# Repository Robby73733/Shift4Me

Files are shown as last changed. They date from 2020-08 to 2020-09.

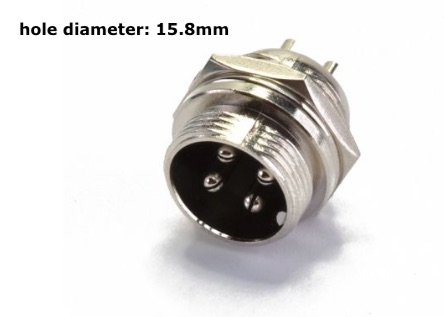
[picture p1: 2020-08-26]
installation/pics_18-22/Pic_22.JPG

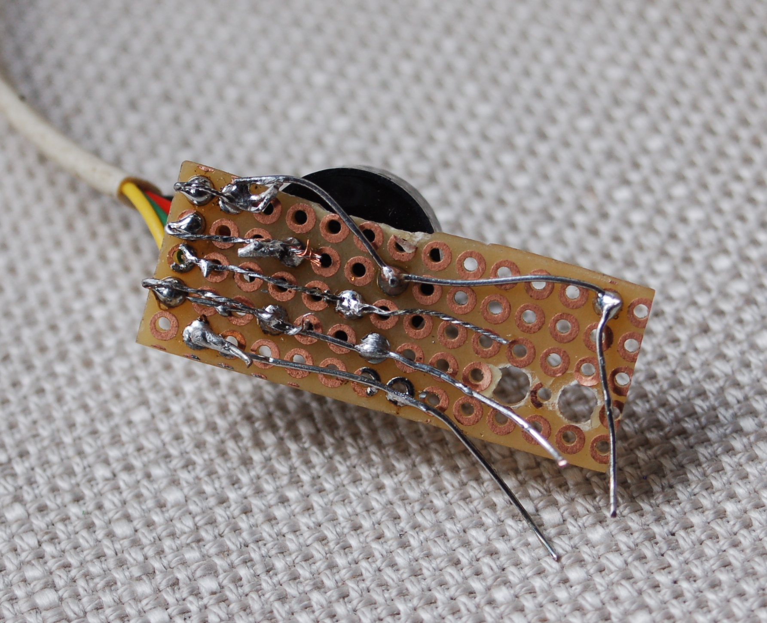
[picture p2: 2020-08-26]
installation/pics_1-17-building-manual/Pic_7.JPG

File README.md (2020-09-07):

# Shift4Me
Automatic Gear Shifting

www.shift4me.com

[heise.de news](https://www.heise.de/news/Shift4Me-Automatische-Fahrradschaltung-mit-Arduino-4873946.html) [2020/08/25]

[chip.de news](https://www.chip.de/news/Fahrrad-Hack-So-bekommt-Ihr-Rad-eine-automatische-Gangschaltung_182934165.html) [2020/08/29]

[Eindhoven Maker Faire](https://eindhoven.makerfaire.com/maker/entry/216/) [26 & 27 september 2020]

Shift4me is designed to be very simple to use. But “under the hood” there’s a lot going on. Apart from the normal handling, this manual will tell you how to adjust some parameters to suit your preferences such as cadence, gear changing speed and much more.
In this manual we’ll use “DG” as short for Derailleur Gears, so with x-amount of sprockets, and “HG” for Hub Gears, with internal gears in the rear wheel.
Don’t forget to post any comments you may have - positive or negative - or feature requests on the forum of the website.

## Contributors

Jan Oelbrandt <info@shift4me.com>

Van Vuong Ngo [vanvuongngo@github](https://github.com/vanvuongngo)

Shift4Me - Automatic Gear Shifting (http://www.youtube.com/watch?v=caMIED0Iqpo "Video: Shift4Me - introduction")

### What?
Shift4Me is a system that you can add to a bicycle. It is an electronic device that shifts your gears, based upon cadence (the rotation of your pedals). Its goal is to keep you in a comfortable gear setting, so your bike ride is comfortable and efficient. You can add a Shift4me to any bicycle that has a single cable (spring return) gearing system - that includes standard “cassette” derailleurs, hubgears (internal gears in the rear wheel axle), that means 95% of the market.

### Why?

The system is in another ballpark than the (getting ever more popular) electric pedal-assist bicycle. It doesn’t add power to gain speed. However, because the system keeps you in the most appropriate gear, it makes you cycle more efficiently. Shift4Me can be added to a non-pedal-assist bicycle, in that aspect it is unique in the world (as far as I know). But if you add it to a pedal-assist bicycle(*) you not only get the most efficient ride and best battery performance, it will also help to reduce wear and maintenance.

### Who?
Shift4Me is intended for cyclists that want to have the most comfortable ride possible without having to worry about shifting to be in the right gear. It is designed to be a “no-brainer”: only a single button is present, and that even doesn’t have to be used if you don’t want to. (the button is actually a dual function button that does “bypass” and “reset”). Just turn the power on and enjoy the ride, that’s the main goal.

### How?
Shift4Me is a do-it-yourself project: it is not available as a finished, ready-to-use system. You have to build it yourself - there’s a comprehensive build manual. Only (reasonably) commonly available components are needed. It is an open-source platform which “techies” can change, improve and experiment upon.
(*) The past years, some companies have been introducing automatic gear shifting to their pedal-assist systems and bicycles.

see [Documents](/documents)

see [Basic Components - Parts list](https://github.com/vanvuongngo/Shift4Me/blob/master/installation/Shift4Me-basic-components.pdf)

# Installation Instructions

Assuming you have the [Arduino IDE](https://www.arduino.cc/) or [Visual Studio Code](https://code.visualstudio.com/) with [PlatformIO](https://www.platformio.org/) installed on your computer.

see [Installation](/installation)

# Maintenance

The whole Shift4Me system is reasonably water-proof. But it is not advisable to leave your bike outdoors all year long.... not only for the Shift4Me...
If the system is installed by capable hands, everything should be virtually maintenance-free. Just don’t leave the power on for too long if you’re not cycling, that will possibly kill the battery. When I go shopping, I leave it on because I don’t like shopping. I’m always in and out of the store in like 10 minutes, so I don’t bother to turn the system off for such a short period of time. After some time of cycling with the system: if you feel that Shift4Me is no longer shifting in the right sprocket of your DG, or it’s shifting in between gears of your HG, then first try to adjust the cable adjusters. In the same way as you would on a non-Shift4Me equipped bicycle. If that doesn’t help, redo the calibrate procedure as described in the Build Manual.

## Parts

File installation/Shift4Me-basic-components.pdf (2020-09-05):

## Bike parts

## Page 1

Item | example URL | Aliexpress URL
Derailleur cable with hose & ends | 7.99 €
cable adjuster | 5.95 €
Sensor | 4.50 €
Magnet | 2.12 €
20.56 €
example price | Aliexpress price

https://www.bikester.be/706991.html

https://www.bikester.be/jagwire-index-adjusting-barrel-kruk-en-trapas-accessoires-zwart-zilver-626630.html

https://www.bikester.be/fietsaccessoires/fietscomputers/fietscomputers-accessoires/321498.html

https://www.conrad.be/p/tru-components-d10t5-m3-permanente-magneet-ring-n35-grenstemperatuur-max-80-c-1568107

## Electronics

## Page 2

Item | recommended brand&type picture example URL | AliExpress URL | price
| | | 14.99 € | 10.67 €
Arduino Nano or 100% compatible | ATmega 328 (code A000005) | | 23.49 € | 2.07 €
Toggle switch (on)off(on) | | | 2.68 € | 5.21 €
PCB board (island contacts) | | | 2.90 € | 1.10 €
2X resistor 470 ohms 1/4W | | | 0.22 € | 0.48 €
resistor 220 ohms 1/4W | | | 0.12 € | 0.48 €
push-button w/ Led | Velleman R1396B | Pic_18.JPG | 4.20 € | 4.20 €
buzzer | | | 0.67 € | 0.84 €
flex multicable | | | 1.16 € | 1.74 €
solid cable | | | 8.95 € | 13.85 €
4-pole cable | | | 0.35 € | 0.35 €
6V accupack | | | 24.49 € | 12.83 €
2.4V accupack | | | 8.18 € | 5.84 €
charger | | | 16.49 € | 16.49 €
servo female connector (or row pin connectors) | | | 3.94 € | 3.94 €
mono jack male plug 3.5mm | | Pic_19.JPG | 2.04 € | 1.58 €
mono jack female chassis 3.5mm | | | 1.40 € | 3.31 €
stereo jack male plug 3.5mm | | | 0.74 € | 0.51 €
stereo jack 3.5 PCB | | | 2.82 € | 2.72 €
charger plug chassis 5.5x2.5mm | | Pic_20.JPG | 3.25 € | 1.92 €
double pole key-switch (19mm diameter) | | Pic_21.JPG | 7.50 € | 3.54 €
DIN chassis male 4-pole | | Pic_22.JPG | 1.75 € | 0.74 €
DIN plug female 4-pole | | | 1.75 € (already incl. In above) | 0.00 €
screw terminals | | | 1.21 € | 1.21 €
1 metal screw 3mm (if the one that comes with the servo is not long enough)
4 self-tapping wood screws to mount the servo (3mm)
6 self-tapping wood screw to mount the BigBox top (2.5mm)
| | | 135.29 € | 95.62 €
* The links above usually are affiliate links which support the project (no additional cost for you).

# price

Servo analog or
Servo digital (low energy)

Power HD 1501MG
Power HD LF-20MG

https://amzn.to/2ExU4gd (17kg analog) https://amzn.to/2YQ52nZ (20kg digital 14.66€)

https://s.click.aliexpress.com/e/_dVdMwgI (17kg analog) https://s.click.aliexpress.com/e/_dSseepa (20kg digital 16.17€)
https://www.conrad.be/p/arduino-board-nano-atmega328-1172623 | https://s.click.aliexpress.com/e/_dZPwkR8
https://www.conrad.be/p/apem-5537a-55370003-tuimelschakelaar-250-vac-3-a-1x-aanuitaan-moment0moment-1-stuks-700351 | https://s.click.aliexpress.com/e/_dTNvhgW (5PC)
https://www.conrad.be/p/rademacher-wr-typ-811-2-printplaat-hardpapier-l-x-b-100-mm-x-75-mm-35-m-rastermaat-254-mm-inhoud-1-stuks-529580 | https://s.click.aliexpress.com/e/_d73hrcW
https://www.conrad.be/p/te-connectivity-rox2sj470r-metaalfilmweerstand-470-axiaal-bedraad-2-w-5-1-stuks-1677278 | https://s.click.aliexpress.com/e/_dYAoMHM (20PC)
https://www.conrad.be/p/te-connectivity-rox3sj220r-metaalfilmweerstand-220-axiaal-bedraad-3-w-5-1-stuks-1676926 | https://s.click.aliexpress.com/e/_dYAoMHM (20PC)
https://www.gotron.be/miniatuur-drukschakelaar-met-rode-led-spst-off-on.html
https://www.conrad.be/p/conrad-components-miniatuurzoemer-geluidsontwikkeling-85-db-spanning-5-v-1-stuks-1511468 | https://s.click.aliexpress.com/e/_dXHzsWI (10PC)
https://www.gotron.be/flatcable-10p-gekleurd.html | https://s.click.aliexpress.com/e/_dWd2n1s (1m)
https://www.gotron.be/soepele-montagedraad-set-90m.html | https://s.click.aliexpress.com/e/_dVI9d3I
https://www.gotron.be/telefoniekabel-4-aders-voor-rj-connectoren-met-afscherming-zwart.html
https://www.conrad.be/p/nimh-accupack-6-v-2200-mah-aa-penlite-z-soldeerlip-emmerich-readytouse-5aa-zlf-255070 | https://s.click.aliexpress.com/e/_d6IRgAs (2PC+Lader 3500mAH)
https://www.conrad.be/p/nimh-accupack-24-v-750-mah-aaa-potlood-z-soldeerlip-panasonic-eneloop-reihe-f1x2-251957 | https://s.click.aliexpress.com/e/_dZB0umg (800mAH)
https://www.conrad.be/p/modelbouw-oplader-220-v-1-a-voltcraft-mw6168v-nicd-nimh-237739
https://www.gotron.be/extra-lange-afbreekbare-vergulde-contacten-16-pins-mannelijk-mannelijk-5-pcs.html
https://www.conrad.be/p/tru-components-jackplug-35-mm-stekker-recht-aantal-polen-2-mono-zwart-1-stuks-1564577 | https://s.click.aliexpress.com/e/_dTggrLQ (2PC)
https://www.conrad.be/p/bkl-electronic-072314-jackplug-35-mm-bus-inbouw-verticaal-aantal-polen-2-mono-zilver-1-stuks-733121 | https://s.click.aliexpress.com/e/_dV7PpWU (10PC)
https://www.conrad.be/p/tru-components-jackplug-3.5-mm-stekker-recht-aantal-polen-3-stereo-zwart-1-stuk-s-1559784 | https://s.click.aliexpress.com/e/_d7M1EzE (5PC)
https://www.conrad.be/p/cliff-fcr1295-jackplug-35-mm-bus-inbouw-horizontaal-aantal-polen-3-stereo-zwart-1-stuks-705830 | https://s.click.aliexpress.com/e/_Bf8PyEsY (10PC)
https://www.conrad.be/p/cliff-scd-026a-laagspannings-connector-bus-inbouw-verticaal-55-mm-25-mm-1-stuks-735627 | https://s.click.aliexpress.com/e/_dZiBm3W (w/ waterproof)
https://www.gotron.be/sleutelschakelaar-dubbelpolig-on-off-2a-250v-d-19mm.html | https://s.click.aliexpress.com/e/_d7c1by8
https://www.gotron.be/4-polige-cb-din-stekker-mannelijk-chassismontage.html | https://s.click.aliexpress.com/e/_dY64CCY (set w/ pastic lid cap)
https://www.gotron.be/4-polige-cb-din-stekker-vrouwelijk-kabelmontage.html
https://www.gotron.be/lusterklem-1-5-6mm-15a-in-latten-van-12-polen.html

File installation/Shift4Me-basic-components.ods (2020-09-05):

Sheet: Bike parts
Item | example URL | example price | Aliexpress URL | Aliexpress price
Derailleur cable with hose & ends | https://www.bikester.be/706991.html | 7.99 €
cable adjuster | https://www.bikester.be/jagwire-index-adjusting-barrel-kruk-en-trapas-accessoires-zwart-zilver-626630.html | 5.95 €
Sensor | https://www.bikester.be/fietsaccessoires/fietscomputers/fietscomputers-accessoires/321498.html | 4.50 €
Magnet | https://www.conrad.be/p/tru-components-d10t5-m3-permanente-magneet-ring-n35-grenstemperatuur-max-80-c-1568107 | 2.12 €
 |  | 20.56 €

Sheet: Electronics
Item | recommended brand&type | picture | example URL | price | AliExpress URL | price
Servo analog or Servo digital (low energy) | Power HD 1501MG Power HD LF-20MG |  | https://amzn.to/2ExU4gd (17kg analog) https://amzn.to/2YQ52nZ (20kg digital 14.66€) | 14.99 € | https://s.click.aliexpress.com/e/_dVdMwgI (17kg analog) https://s.click.aliexpress.com/e/_dSseepa (20kg digital 16.17€) | 10.67 €
Arduino Nano or 100% compatible | ATmega 328 (code A000005) |  | https://www.conrad.be/p/arduino-board-nano-atmega328-1172623 | 23.49 € | https://s.click.aliexpress.com/e/_dZPwkR8 | 2.07 €
Toggle switch (on)off(on) |  |  | https://www.conrad.be/p/apem-5537a-55370003-tuimelschakelaar-250-vac-3-a-1x-aanuitaan-moment0moment-1-stuks-700351 | 2.68 € | https://s.click.aliexpress.com/e/_dTNvhgW (5PC) | 5.21 €
PCB board (island contacts) |  |  | https://www.conrad.be/p/rademacher-wr-typ-811-2-printplaat-hardpapier-l-x-b-100-mm-x-75-mm-35-m-rastermaat-254-mm-inhoud-1-stuks-529580 | 2.90 € | https://s.click.aliexpress.com/e/_d73hrcW | 1.10 €
2X resistor 470 ohms 1/4W |  |  | https://www.conrad.be/p/te-connectivity-rox2sj470r-metaalfilmweerstand-470-axiaal-bedraad-2-w-5-1-stuks-1677278 | 0.22 € | https://s.click.aliexpress.com/e/_dYAoMHM (20PC) | 0.48 €
resistor 220 ohms 1/4W |  |  | https://www.conrad.be/p/te-connectivity-rox3sj220r-metaalfilmweerstand-220-axiaal-bedraad-3-w-5-1-stuks-1676926 | 0.12 € | https://s.click.aliexpress.com/e/_dYAoMHM (20PC) | 0.48 €
push-button w/ Led | Velleman R1396B | Pic_18.JPG | https://www.gotron.be/miniatuur-drukschakelaar-met-rode-led-spst-off-on.html | 4.20 € |  | 4.20 €
buzzer |  |  | https://www.conrad.be/p/conrad-components-miniatuurzoemer-geluidsontwikkeling-85-db-spanning-5-v-1-stuks-1511468 | 0.67 € | https://s.click.aliexpress.com/e/_dXHzsWI (10PC) | 0.84 €
flex multicable |  |  | https://www.gotron.be/flatcable-10p-gekleurd.html | 1.16 € | https://s.click.aliexpress.com/e/_dWd2n1s (1m) | 1.74 €
solid cable |  |  | https://www.gotron.be/soepele-montagedraad-set-90m.html | 8.95 € | https://s.click.aliexpress.com/e/_dVI9d3I | 13.85 €
4-pole cable |  |  | https://www.gotron.be/telefoniekabel-4-aders-voor-rj-connectoren-met-afscherming-zwart.html | 0.35 € |  | 0.35 €
6V accupack |  |  | https://www.conrad.be/p/nimh-accupack-6-v-2200-mah-aa-penlite-z-soldeerlip-emmerich-readytouse-5aa-zlf-255070 | 24.49 € | https://s.click.aliexpress.com/e/_d6IRgAs (2PC+Lader 3500mAH) | 12.83 €
2.4V accupack |  |  | https://www.conrad.be/p/nimh-accupack-24-v-750-mah-aaa-potlood-z-soldeerlip-panasonic-eneloop-reihe-f1x2-251957 | 8.18 € | https://s.click.aliexpress.com/e/_dZB0umg (800mAH) | 5.84 €
charger |  |  | https://www.conrad.be/p/modelbouw-oplader-220-v-1-a-voltcraft-mw6168v-nicd-nimh-237739 | 16.49 € |  | 16.49 €
servo female connector (or row pin connectors) |  |  | https://www.gotron.be/extra-lange-afbreekbare-vergulde-contacten-16-pins-mannelijk-mannelijk-5-pcs.html | 3.94 € |  | 3.94 €
mono jack male plug 3.5mm |  | Pic_19.JPG | https://www.conrad.be/p/tru-components-jackplug-35-mm-stekker-recht-aantal-polen-2-mono-zwart-1-stuks-1564577 | 2.04 € | https://s.click.aliexpress.com/e/_dTggrLQ (2PC) | 1.58 €
mono jack female chassis 3.5mm |  |  | https://www.conrad.be/p/bkl-electronic-072314-jackplug-35-mm-bus-inbouw-verticaal-aantal-polen-2-mono-zilver-1-stuks-733121 | 1.40 € | https://s.click.aliexpress.com/e/_dV7PpWU (10PC) | 3.31 €
stereo jack male plug 3.5mm |  |  | https://www.conrad.be/p/tru-components-jackplug-3.5-mm-stekker-recht-aantal-polen-3-stereo-zwart-1-stuk-s-1559784 | 0.74 € | https://s.click.aliexpress.com/e/_d7M1EzE (5PC) | 0.51 €
stereo jack 3.5 PCB |  |  | https://www.conrad.be/p/cliff-fcr1295-jackplug-35-mm-bus-inbouw-horizontaal-aantal-polen-3-stereo-zwart-1-stuks-705830 | 2.82 € | https://s.click.aliexpress.com/e/_Bf8PyEsY (10PC) | 2.72 €
charger plug chassis 5.5x2.5mm |  | Pic_20.JPG | https://www.conrad.be/p/cliff-scd-026a-laagspannings-connector-bus-inbouw-verticaal-55-mm-25-mm-1-stuks-735627 | 3.25 € | https://s.click.aliexpress.com/e/_dZiBm3W (w/ waterproof) | 1.92 €
double pole key-switch (19mm diameter) |  | Pic_21.JPG | https://www.gotron.be/sleutelschakelaar-dubbelpolig-on-off-2a-250v-d-19mm.html | 7.50 € | https://s.click.aliexpress.com/e/_d7c1by8 | 3.54 €
DIN chassis male 4-pole |  | Pic_22.JPG | https://www.gotron.be/4-polige-cb-din-stekker-mannelijk-chassismontage.html | 1.75 € | https://s.click.aliexpress.com/e/_dY64CCY (set w/ pastic lid cap) | 0.74 €
DIN plug female 4-pole |  |  | https://www.gotron.be/4-polige-cb-din-stekker-vrouwelijk-kabelmontage.html | 1.75 € | (already incl. In above) | 0.00 €
screw terminals |  |  | https://www.gotron.be/lusterklem-1-5-6mm-15a-in-latten-van-12-polen.html | 1.21 € |  | 1.21 €
1 metal screw 3mm (if the one that comes with the servo is not long enough)
4 self-tapping wood screws to mount the servo (3mm)
6 self-tapping wood screw to mount the BigBox top (2.5mm)
 |  |  |  | 135.29 € |  | 95.62 €
* The links above usually are affiliate links which support the project (no additional cost for you).

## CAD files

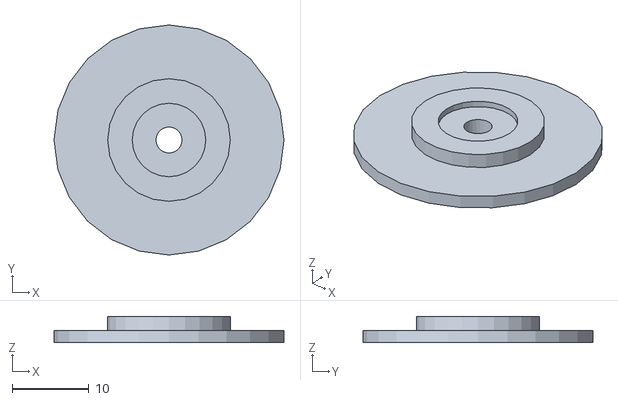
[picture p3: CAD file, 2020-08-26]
installation/3D-prints/ServoHorn_Derailleur-16.stl
30.0 x 30.0 x 3.40

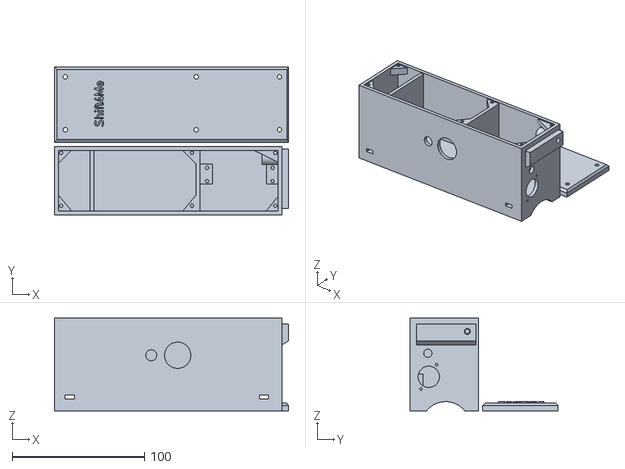
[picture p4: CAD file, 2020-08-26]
installation/3D-prints/BigBox.stl
177.0 x 112.0 x 70.0

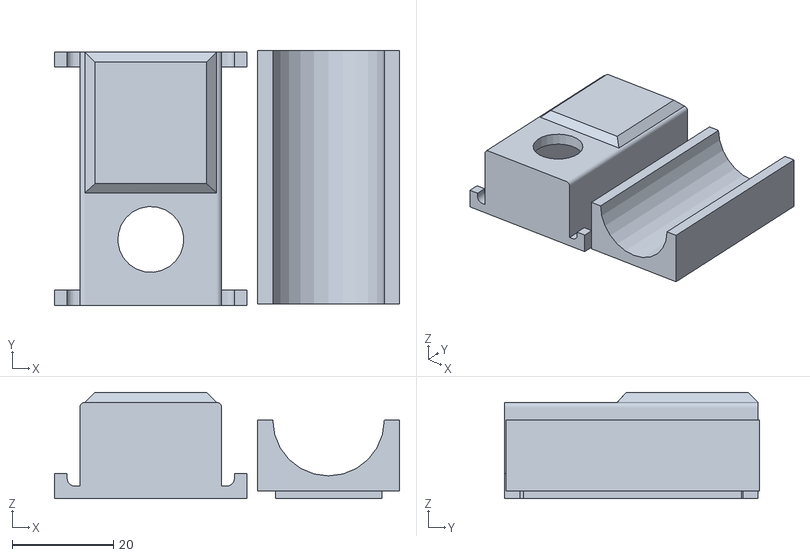
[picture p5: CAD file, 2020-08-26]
installation/3D-prints/ControlUnit.stl
68.1 x 50.2 x 21.0

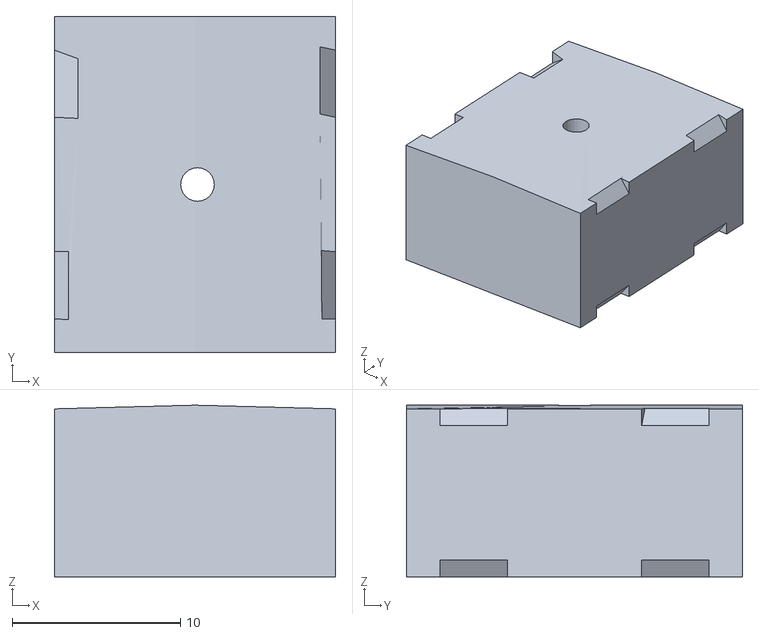
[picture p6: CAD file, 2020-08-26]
installation/3D-prints/MagnetHolder.stl
16.7 x 20.0 x 10.2

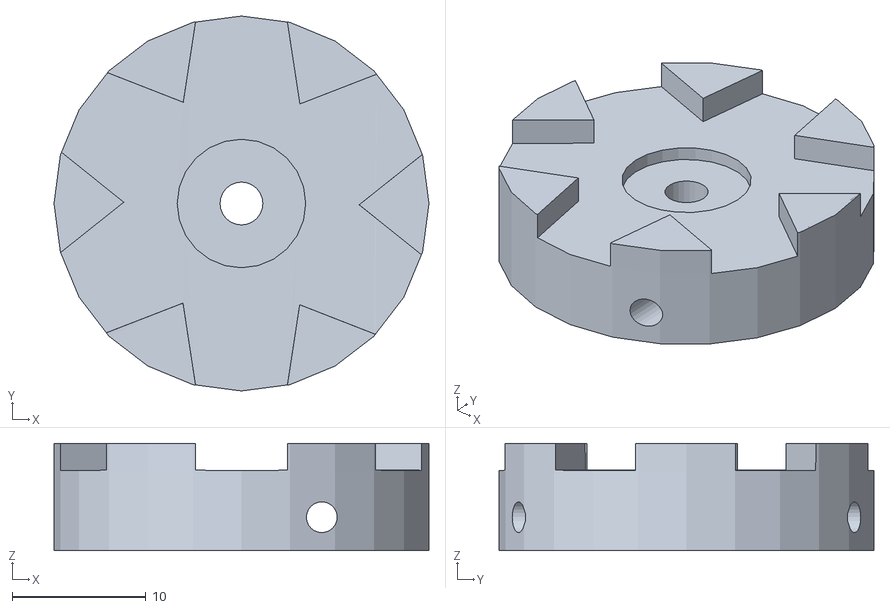
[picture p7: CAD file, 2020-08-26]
installation/3D-prints/ServoHorn_HubGear.stl
28.0 x 28.0 x 8.02

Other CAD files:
installation/3D-prints/ServoHorn_Derailleur-15.stl

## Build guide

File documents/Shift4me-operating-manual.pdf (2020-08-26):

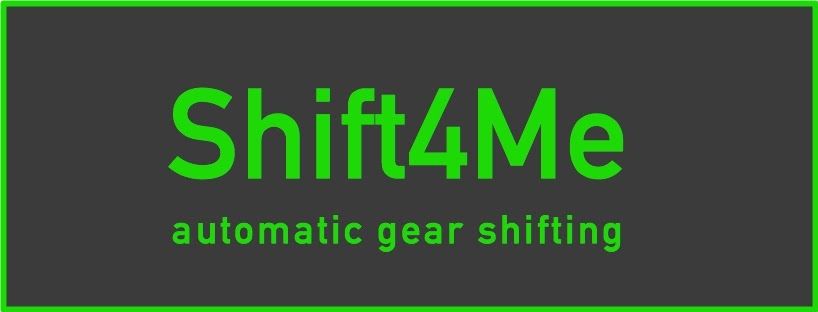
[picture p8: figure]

## Operating manual v1.0

### Introduction

Shift4me is designed to be very simple to use. But “under the hood” there’s a lot going on. Apart from the normal handling, this manual will tell you how to adjust some parameters to suit your preferences such as cadence, gear changing speed and much more.
In this manual we’ll use “DG” as short for Derailleur Gears, so with x-amount of sprockets, and “HG” for Hub Gears, with internal gears in the rear wheel.
Don’t forget to post any comments you may have - positive or negative - or feature requests on the forum of the website.

### Taking a ride

The system comes pre-installed with settings that will suit the average cyclist. So once your system is mounted and the battery is charged, you’re good to go.
- Start
Turn the power on using the Key. You’ll probably hear the servo motor turning to its start position, you’ll also see the LED lighting up. Just get on your bike and start cycling. If you have DG, don’t put much pressure on the pedals from the start. This is because your chain might not be in the starting sprocket. The chain doesn’t like it much when you put a lot of strain on it while it is not aligned to the right sprocket.
When you start cycling, you’ll immediately feel that Shift4Me will try to adjust the gears so that you turn your feet in a comfortable cadence. You’ll hear the buzzer sound when it’s adjusting.
- While riding
In fact, you just have to cycle and the system will make sure you’re in the right gear. However, if you understand how the system works, you’ll be able to understand some of the behaviour and to (optionally) fine-tune it to your preferences.
Shift4Me is constantly monitoring your cadence. So when you turn a slow cadence, it’s assuming you’re going uphill or facing some (aarrr!) wind resistance. So it will change to a lighter gear to get a nice, moderate cadence. The same with the opposite: when turning a fast cadence, the system assumes you’re having no trouble at all to turn the pedals, so it will put you in a heavier gear to gain speed.

What if you are really going steep downhill? Most cyclists will stop turning their pedals and enjoy the effortless ride. No problem with Shift4Me: it will recognize you have stopped pedalling and will do the same (nothing…).
If you’re the sporty type of rider, you sometimes might like to lift from your seat and do a little sprint. At that moment, you’ll want to avoid that the Shift4Me will change gears. Use the button (release it when you hear the buzzer-beep) to “bypass” the system for 5 seconds.
- Stopping during your trip
If you’re cycling in city areas, you’ll probably have to stop frequently for traffic lights and those other utilisers of the road (please do not mock them for not having a Shift4Me-equipped bike - stay polite). The system will recognise when you’re “stalling” and will do nothing. When you restart your ride, it will hold action for a bit. This is to avoid unwanted gear shifting while restarting your ride.
But Shift4Me has no way of telling that you have stopped pedalling (on that downhill) or you have stopped for the street-crossing granny. This is where the reset-button comes in: it is very comfortable to be in a light starting gear after a full stop. The reset function is activated by the button (hold it for 2 seconds - that is until you hear the second buzzer-beep). On HG, you can reset while standing still. On DG, it’s better to do that while pedalling (so before you come to a full stop). Remember: this reset-action is just optional. You don’t have to do anything but you can.
- Parking or stopping
It couldn’t be easier: just stop your ride. But don’t forget to turn the power off...

### How far can you go?

The battery has enough power to keep going for a minimum of 5 hours. Because of the minimal design, there’s no real way of telling how much the battery is drained. But it will warn you (the LED will flash periodically) when it is time to charge. When it first starts flashing, that means you still will be able to do 30 minutes of cycling. So don’t worry, you’ll get home without a problem in most cases. If it is flashing constantly, you only have about 10 minutes left.
When the battery is fully drained, the servo will not be able to pull the cable anymore. Your gears will be in their lightest (HG) or heaviest (DG) setting...

### Adjusting preferences

Assuming you have the Arduino IDE installed on your computer (or you’re using the web-version): open your personal script for your Shift4Me system.
Click the “preferences-ride” tab as you see in this pic:

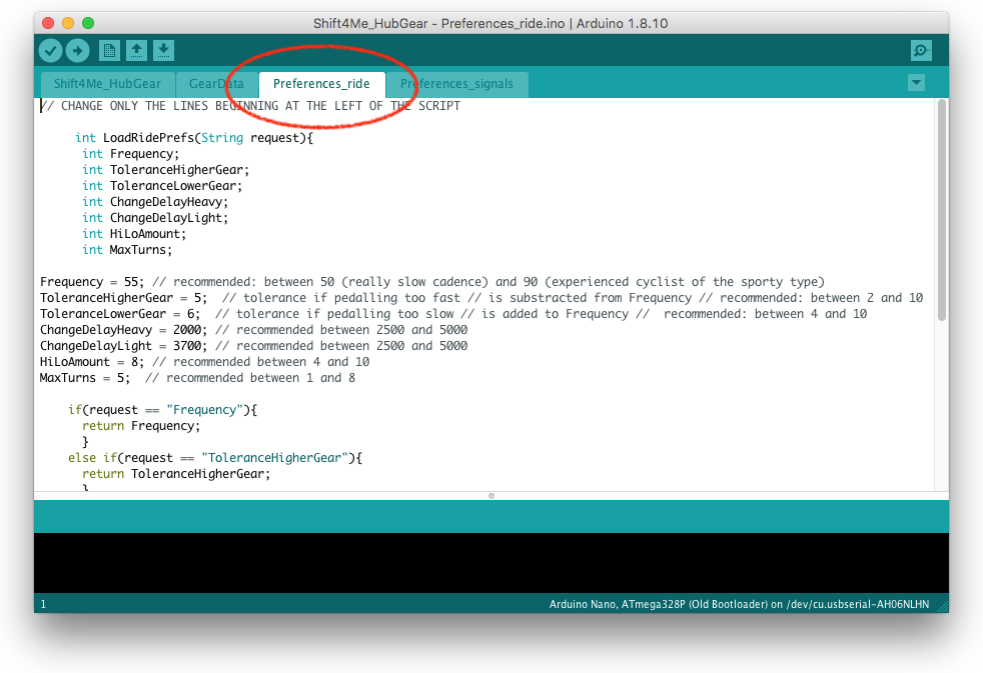
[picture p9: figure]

From this moment, be careful: even a small syntax error can make the script unusable. As always, it’s a good idea to make a backup copy of your script before you start editing.
There are 7 settings you can edit. All of them are located to the far left of the script window. If you try to change anything that is not located there, I can not be held accountable for the consequences… These 7 parameters should be round figures (so don’t use commas or full stops) and should end with a semicolon. A double slash can be used (and you see them already in the script) to write comments in the script. What I often do, when adjusting parameters, is to copy the line that I will edit and make it inactive with a double slash. This is kind of a backup in the script itself, and makes it easy to revert to old settings.
1. “Frequency”
This is your preferred cadence. This is the figure the system aims for, the rotations per minute your feet turn while cycling. Without a doubt, this is the most important parameter. See the pic below… You’ll see the other parameters following.

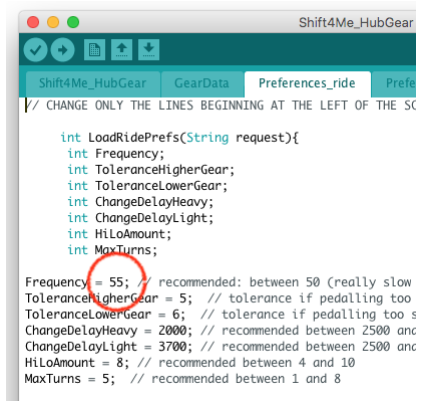
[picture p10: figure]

2. “ToleranceHigherGear”
Because there has to be a tolerance for the cadence (how long you think you can keep it up, turning exactly 55 RPM?) you can adjust this. I found out during testing that it is great to have a separate figure for the tolerance change-to-a-lighter-gear than the other way, so there are 2 parameters for this. So for example you set your Frequency to 55, and your ToleranceHigherGear to 5, the system will only put you in a lighter gear if you’re turning less than 50 RPM. If you set ToleranceHigherGear to 8, it will react if you’re doing less than 47 RPM. You get, don’t you?
3. “ToleranceLowerGear”
The same as point 2, but for the above limit...
4. “ChangeDelayHeavy”
Because it would be annoying that the system would react immediately once a non-preferred RPM is read by the Sensor, there is a parameter to adjust this. This figure is in milliseconds. It is a parameter that has an effect on how often the system will change gears: if it changes too often, that’s annoying. If it changes not often enough, that’s annoying too...
5. “ChangeDelayLight”
This ChangeDelay is also separately adjustable for lighter and heavier gearing...
6. “HiLiAmount”
Please disregard this, that dates from a pre-release version.
7. “MaxTurns”
This is just a parameter that overrides the ChangeDelay. It is for these rare occasions that you are able to turn the pedals madly fast. When that happens, you don’t want to wait 3 seconds to be in a more comfortable gear: you want the gears changed NOW!

### Charging the battery

Take your battery charger. Make sure the plug is center-positive and it is set to “7 cells (8.4V) NiMh”. The more current you allow the faster your battery will be charged. I recommend charging at 500mA.

Make sure your Shift4Me is turned off before you plug the charger into the socket.
When you plug it in your Shift4Me, first go through the “discharge” cycle - see your charger manual to do this. Once that is done, begin charging. (most chargers will automatically start charging once the discharging is done)
Charging will be complete after 8 hours. Then simply unplug the charger from the Shift4Me.

### Maintenance

The whole Shift4Me system is reasonably water-proof. But it is not advisable to leave your bike outdoors all year long…. not only for the Shift4Me…
If the system is installed by capable hands, everything should be virtually maintenance-free. Just don’t leave the power on for too long if you’re not cycling, that will possibly kill the battery. When I go shopping, I leave it on because I don’t like shopping. I’m always in and out of the store in like 10 minutes, so I don’t bother to turn the system off for such a short period of time. After some time of cycling with the system: if you feel that Shift4Me is no longer shifting in the right sprocket of your DG, or it’s shifting in between gears of your HG, then first try to adjust the cable adjusters. In the same way as you would on a non-Shift4Me equipped bicycle. If that doesn’t help, redo the calibrate procedure as described in the Build Manual.

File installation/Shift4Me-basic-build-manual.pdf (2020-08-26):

# Shift4Me build manual

Introduction
So, you’re planning on building a Shift4Me? Great! It’s fun to do and even greater to ride your bike once it’s installed. Before you go any further, please read through this little introduction to avoid disappointments.

First of all: this manual can be used if you want to build a Shift4Me as you see in the demo video’s on the website. If you want to build one that is different(*) just get the “PCB” file and start from there. Or maybe you want another design of the BigBox? Then just disregard the 3Dprint section and mount the system in your own fashion.

Building a Shift4Me is pretty straight-forward if you have (intermediate) soldering skills, you are (a little bit) familiar with Arduino programming and you have (some) experience on bicycle mechanics. Oh, you don’t? Then there’s two options: 1-just go ahead but be prepared for some trial-and-error. 2-pick up the phone and contact someone who has the experience. Don’t be shy
- I’m sure all handy people you know will be glad to help out with this fun project.

What you’re getting yourself into is:
- Print the 3D parts
- Shop for parts
- Solder everything
- Test connections
- Install everything on your bike
- Surprise your neighbours with your self-build auto-gearing bicycle

Building a Shift4Me is going to cost you about 120 euro/USD in parts (excluding the bike itself of course), and is going to take you about two days to finish. The reward will be an automatic-gearing bicycle that is fun to ride.
A complete step-by-step build manual is yet to be finished. This one just has the basics covered.
Don’t forget to post your experiences on the forum of the Shift4me website!

Have fun!

Jan Oelbrandt
Shift4Me developper

* People often ask me “Why don’t you add a LCD screen, to display the current gear, battery status, and so on?” and things like “Add a speedometer, that would be a big improvement.” I don’t disagree with them, but I do have my reasons for not doing this (see the “Shift4Me introduction”). But if you want to add bells and whistles to Shift4me: who’s gonna stop you? Just go ahead!

Content
Before you start
1. Prepare your bike
2. Get your stuff together
3. Prepare the Arduino

Build the thing!
4. 3D printing jobs
5. Assemble and solder the main PCB
6. Solder the plugs
7. Assemble and solder the control PCB
8. Solder the TestSwitch
9. Mount everything in the BigBox
10. Run some tests

Installation
11. Install the BigBox on your bike
12. Connect your hub gear or derailleur to the BigBox
13. Install the Control unit, the Sensor and the magnet
14. Tune the system to your bike
15. Upload the Shift4Me script

Appendix

1. Prepare your bike
Make sure you have a good working bicycle ready. That means: aside from basics such as good brakes, proper tires etc. it should have a smoothly shifting and correct handling gearing system. Any bike with a standard derailleur (any amount of sprockets) or a hub gear (any amount of gears) will do, as long as it’s in working order. Only gearing systems using a single-cable control, spring-return can be used (that means: no Rohloff equipped bike, sorry folks!).
Don’t dismantle anything yet on the bike, let’s build the Shift4Me first.
2. Get your stuff together
a. Tools
i. Soldering iron & lead to… solder
ii. | Pliers to mount the plugs
iii. | A clean desk
iv. | A multi-meter. Preferably one that has a beep-function for testing zero
| ohm (contact test)
v. A computer with the Arduino software installed (the IDE). Feel free to
| choose the desktop or the online version. https://www.arduino.cc/
| Preferably a laptop, since it’s going to be necessary to have it nearby your
| bike during setup. Remember: when using the local version, all script files
| have to be present in the right folder on your computer. See
| www.arduino.cc for all documentation.
b. Components
| You need all the items to build the Shift4Me described in the “basic
| components” pdf file. The BigBox is designed to accommodate various
| connectors. If you want to use other types of connectors, redraw the
| BigBox’s STL file first.
c. PCB layout, routing info etc… It’s all in the PDF files called “PCB” and “schematic” in the Downloads on the Shift4Me website.
d. Get the STL files to be able to 3D-print the BigBox, the control unit and the magnet holder. They’re in the “3D-prints” zip file in the Downloads.
e. Get the right STL file for the servo horn to match your gearing system (Hubgear or Derailleur)
f. Download the Arduino scripts from the “Scripts” zip file (again: choose Hubgear or Derailleur)
3. Prepare the Arduino a. Shift4Me is designed around an Arduino Nano. If you want to use an other board, you’re on your own to redesign the PCB. The required specs, if you choose an other board, can be found in the Appendix below.
b. Unpack the Arduino Nano board and connect it to your computer. The power-LED should light up on the board. Now startup the Arduino IDE and upload the test script called “Blink”. You don’t have to download it seperately, it is under the “File->Examples->Basics” menu in the IDE. Once uploaded, an other LED on the board should go on and off repeatedly.
i. Does it work? Is the LED of your board blinking as it should? OK then, proceed to step 3.
ii. | No luck? No blinking LED? Error messages popping up in the Arduino
| IDE? Don’t worry, there’s a whole community of Arduino users ready to
| help you at www.arduino.cc (if you don’t find what you need on the
| Shift4Me forum)
c. Get your Script files from the website if you haven’t already done so. There a 3 script you’re going to use: “tester”, “calibrate” and also the appropriate script for your gearing system (“hubgear” or “derailleur”). Don’t forget: if working locally, these should be in the right folder on your computer.
4. 3D print the BigBox, the ServoHorn, MagnetHolder and the ControlUnit
a. All parts that have to be printed are in STL format. They first have to be saved as GCODE files, and a slicing software has to make sure that all overhangs are taken care of. If you’re new to 3D-printing, please let someone assist you. Even better: contact your local 3D-printservice, they’ll take care of everything.
b. Printing material: PLA is fine. You can print everything solid, but hollow fine-mesh is sufficient.
c. When printing is done, remove all support material (if the 3D-printservice hasn’t already done so). Make sure you free the rectangular holes in the bottom of the BigBox, two tie-wraps will have to be able to feed through them.
d. Check if these components will fit in the holes:
i. For the ControlUnit - the LED/button combo
ii. | For the BigBox: side wall: the ChargerPlug and the KeySwitch.
| Front wall: cable adjuster, female mini-jack chassis &
| male DIN-chassis.
5. Assemble and solder the main PCB content will be available in the yet-to-be-completed manual -
6. Solder plugs
content will be available in the yet-to-be-completed manual -
7. Assemble and solder the control PCB
- content will be available in the yet-to-be-completed manual -
8. Solder the TestSwitch
- content will be available in the yet-to-be-completed manual -
9. Mount everything in the BigBox
- content will be available in the yet-to-be-completed manual -

10. Run some tests
a. Test for wanted and unwanted circuit lines. Perform these steps using a ohm-meter or cable tester. (“short”=contact=0ohm and “NC”=no contact=infinite ohm). Set the KeySwitch to the “off” position. If you’re not sure which position that is, use your multimeter to determine (Key#1-Key#2 should NC). Also, connect the ControlUnit to the BigBox with the DIN connector
b. You should have a “short” between the following. GND is the looped wire on your main PCB.
i. GND -> mini jack outer shell
ii. | GND -> screw terminal #2
iii. | GND -> point#21
iv. | GND -> charge plug outer shell (with the charger plugged in)
v. GND -> ServoPlug (black or brown wire)
vi. screw terminal #3 -> charge chassis tip
c. You should have NC between the following:
i. screw terminal #1 and any of the Arduino pins
ii. | screw terminal #3 and any of the Arduino pins
iii. | Charge chassis outer shell -> charge chassis tip
iv. | Between any of the 3 screw terminals
v. screw terminal #1 -> ServoPlug, middle leg (red wire)
d. Now turn the key to the “On” position. You should have a “short” between screw terminal #1 -> ServoPlug, middle leg (red wire).
e. DO NOT PROCEED if any of the above failed. If something turned out wrong, check for sloppy soldering, broken wires, etcetera.
f. If you want to do additional checking, you can measure all the points of the Arduino to where they should “short”.
g. Almost done… you’re ready now to run the TestScript. First, connect the Sensor and keep the magnet ready. Also plug the TestSwitch in the mini-jack plug on the main PCB. Now connect the Arduino to your computer using an USB cable and upload the script called “Shift4Me_Tester”. Immediately after you’ve done that:
i. The buzzer should sound in a sequence
ii. | The led should light up (flashing)
iii. | Now display the Serial Monitor in the IDE. Now you can monitor the
| activity of the Sensor (hold your magnet on and off nearby the Sensor)
| and the TestSwitch. Also you can push the button on your
| ControlUnit. Everything should read out accordingly in the Serial
| Monitor. The “battery status” should read no more than 4V. See pic 9 for
| an example.
h. If everything reads out fine in the Serial Monitor and you heard the Buzzer, saw the LED flashing, you can now upload the “Calibrate” script. After that, test signals will stop and you can finish the mounting in the BigBox. Unplug the TestSwitch, the Sensor and DIN plug.

i. Put some non-conductive damping material to secure the Main PCB. Use some foam or a piece of garbage cloth.
ii. | Solder 8cm of thick wire to your battery packs (red=positive,
| black=negative). Tape them up to prevent shortcutting to the components.
| BEWARE: don’t shortcut a battery pack, that can lead to accidents. Strip
| one wire at a time!
iii. | Take the 6V battery pack and connect its positive side to the
| negative side of the 2.4V pack, screw them in screw terminal #1
iv. | Screw the red wire from the 2.4V pack to screw terminal #3
v. Take a fourth screw terminal (mark it… #4) and use it to screw the
| black of the 6V pack to the only loose wire left (the thick black one).
i. No fire? No explosion? Then proceed… Plug the USB back into the mainPCB and connect the TestSwitch. Now open the Serial Monitor in the Calibrate script. Put the KeySwitch in the “on” position. Now when you flip the TestSwitch to one side, you should see the “servo pulsewidth” value going up while the servo should rotate in small steps. And have you guessed? The value should go down (the servo rotating in the other direction) when you flip the other side of the TestSwitch. Battery value should be well over 7V (if not, you’ll have to charge first). See screenshot as in pic 10. All going well? Then leave the system in the state of “you reached the minimum position of the servo”.
11. Install the BigBox on your bike
a. Find a suitable place to mount the BigBox to your bike. Keep in mind that, once it is mounted:
i. You have to be able to connect to the USB port of the Arduino.
ii. | The routing of the derailleur cable (that will go from the front of the
| BigBox to your derailleur or hubgear) is neat. That means: as little bends
| as possible and not interfering with moving parts while riding.
b. Take two tie-wraps, feed them through the holes in the bottom of the BigBox and secure the BigBox to a bar of your bike. I like to mount it on the upright bar and I use a piece of old inner tube that I put at the back to protect the paint. See pic 11
12. Connect your hub gear or derailleur to the BigBox
a. If you have a bike stand to lift the complete bike, put it up there. If not, think of a way to hang up the bike to the (back) wheel can turn.
b. If you have a hubgear, it’s a good idea to manually shift down (full cable release), then disconnect the cable with the fixing screw still attached, and write down the distance between center of the fixing screw and the end of the hose. For example: with Shimano Nexus 8 this distance is 10cm. When mounting the new cable, you’ll need this.
c. Dismount the complete manual derailleur cable from your bike.
d. Take a new derailleur cable that’s long enough (duh!) to go from the BigBox to your derailleur or hubgear. The hose: long enough to go from the BigBox to a fixed point of your bike (see pics 12 and 13)

e. Installation of the cable to the ServoHorn is different because of the different design for derailleur vs. hubgear.
i. Hubgear: Feed the cable through the ServoHorn, see pic 16. Feed it all the way so that the ball end is at the horn, see pic 14.
ii. | Derailleur: Feed the cable through the round spline that came along with
| the servo and mount it to the servo together with the ServoHorn, see pic
| 17.
f. Be careful to position the ServoHorn and the round (derailleur) or 6-tooth (hubgear) part so the cable is positioned as in pic 14. Also, the servo must be in “minimum position”. If you’re not sure, just turn the Shift4Me on (using your key) and it will set the servo at minimum position. Now feed the cable from the inside of the BigBox through the cable adjuster (sometimes it’s easier if you screw it off fist, then feed the cable through, and screw the adjuster back on)
g. Feed the cable through the hose (don’t forget the hose ends!). The hose should slide easily over the cable. Apply some grease.
h. Turn the Shift4Me on and plug in your Testswitch.
i. Make sure your the cable adjuster at the BigBox and the cable adjuster on your derailleur (you probably don’t see one if you have a hubgear) are screwed in all the way.
j. Pull the cable and screw/fix it to your derailleur or hubgear.
k. Now flip the TestSwitch so the servo begins to turn counterclockwise in small steps. Your derailleur or hubgear should start moving too as the cable is pulled by the servo. When you have a derailleur, your pedals need to be turning as the derailleur moves to a larger sprocket. With hubgears, this is not necessary.
13. Install the Control unit, the Sensor and the magnet
a. Take two rubber bands and fix the ControlUnit to your handle bar. Lead the wire to the BigBox and connect the DIN plug.
b. Screw the magnet to the magnet holder. Use two small tie-wraps to mount it to the inside of your left pedal.
c. Solder the mono mini-jack plug to the Sensor, leave plenty of cable to reach the BigBox.
d. Take one rubber band and mount the Sensor to the left horizontal bar. When you turn the pedals, the magnet should go past the Sensor with a distance of no more than 5mm. Plug the Sensor (the mini-jack plug, that is) in the BigBox.
14. Tune the system to your bike
a. It’s a good idea, now that everything’s connected, to test the system once more. So take your laptop and put it close to the bike, connect via USB. Upload the TestScript you have used in section 10.g. Open the Serial Monitor, it should read “hall triggered” when you turn the pedals, you see the LED flashing and hear the buzzer. When flipping the TestSwitch, it should read "manual switch position: pull (or release) cable".

b. Now disconnect the Sensor plug from the BigBox and upload the “Calibrate” script. Leave the USB connected. Display the Serial Monitor.
c. Flip the TestSwitch until the derailleur cable it fully pulled (*). This is different for derailleur vs hubgear bikes:
i. When fully pulled, a derailleur will be where the chain is in the largest sprocket (smallest gear).
ii. When fully pulled, most hubgears will be in the highest gear.
d. At this point, when the cable is fully pulled, your Serial Monitor should be around 2300 up to 2400 pulsewidth. If this is a lot lower (say, 1800), your cable needs to be loosened. If the monitor displays “maximum reached” and your cable is not fully pulled, then you need to use one or both of the cable adjusters to tighten it up. (*) fully pulled means: your derailleur is at the maximum of its travel.
e. Success? Then let’s check if your range is covered. Flip the TestSwitch over until the servo is in minimum position, your derailleur should be in the beginning of its travel. OK? Then flip the switch over until the servo is in maximum, and guess what? Your derailleur should be in maximum position. If this fails, you can try to fool around with the cable adjusters. If that still fails, you’ll have to 3Dprint a ServoHorn of a bigger diameter to cover a wider range. In my test bikes, If have a 16mm diameter for a 9-speed Shimano sprocket, and a 28 diameter for a Shimano Nexus8 hubgear. This is because the travel (distance of cable movement) is different.
f. If you can cover the whole range of your gears, then you can move on to tune the gears. Again, this is different for derailleur (see 14.h) vs. hubgears (see 14.g):
g. For Shimano 7-8 speed hubgears it is very easy, because they have a fixed “spacing” and both calibrate in gear#4.
i. Upload the script called “Hubgear” to the Arduino. When done, Turn the
| system on. The servo is now in “starting gear” which is also the calibrate
| position for the Shimano hubgear. There are two yellow line in the hub
| that should line up. If not, adjust the cable adjusters until they do.
ii. | The “Hubgear” script is loaded with the right parameters for a Shimano
| Nexus 8-speed. If you have a 7-speed: you’ll have to find the right
| settings for the servo pulsewidth using the 14.h method. If you have
| another brand of hubgear, make sure you know what the gear number is
| that is used to calibrate the hub - refer to your manufacturers manual -
| and follow the 14.h method.
h. For derailleur gears (each model has its own derailleur travel vs. cable travel relation), you have to write down the pulsewidth you can observe in the Serial Monitor. Make sure you still have the Calibrate script uploaded. When you flip the TestSwitch (start at minimum position, then go up), then flip it step by step until your derailleur makes the chain go in the next gear. It is does, write down the pulsewidth. Do this for every gear, then proceed to the last step.
15. Upload the Shift4Me script a. Run the appropriate script for your gearing system (“hubgear” or “derailleur”). It’s a good idea to immediately save it as a new file (Save as…->choose a new filename) because the script itself will be containing the settings that are unique to your bicycle.
b. With the script opened, you see four tabs in the script window. Go to the second one called “GearData”. It now should look like pic 15.
c. There are two things you need to set here:
i. The amount of gears your bike has (for example: 9 gears). You have to input this figure in the “GearAmount” parameter, see the top red arrow in pic 15..
ii. The pulsewidth figures (bottom red arrow in pic 15) you have obtained in
step 14.h. Put these in ascending order (for derailleurs) or descending
| order (for hubgears) in the gear parameters. Make sure you adjust the
| index value (see green arrow in pic 15) as you need to add or remove
| lines to match your amount of gears. If this is your first encounter with
| scripts: be careful! If you get one digit, semicolon or something else
| wrong the script will not work! If you’re new to this, make a copy of the
| original script so you can always start over easily.
iii. | The gear parameters start counting at zero… So for example if you have
| a 6-gear bike, your GearAmount will be 6 and the parameters will count
| from Gears[0] to Gears[5].
d. When all pulsewidth parameters, and the GearAmount, are set: upload the script to the Arduino.
e. Now put the bike on a stand (if it’s not still there) and test the Shift4Me: plug in the TestSwitch, but don’t plug in the Sensor. Turn the power on using the KeySwitch. Rotate the pedals, and briefly flip the TestSwitch to one side. Your bike gears should move to another gear. Turn the TestSwitch to the other side, guess what? It’s returning to its former gear. If this is all going well, you just have to unplug the TestSwitch, plug in the Sensor, and screw the top onto the BigBox. Congrats, you are now the proud owner of an automatic-gearing bike!

# Appendix

Components for the standard Shift4Me system.
Below is the list of all you need. There’s a file in the Forum’s Downloads “components” too. The only thing you’ll have to work out locally is the printing of the 3D-printed parts, be sure to check the file called “xxx” in the Downloads section if you contact your local 3D printservice, or are going to print the parts on your own printer.

Bike parts
- Derailleur cable with hose. Length depends on where you want to install the BigBox, but xxx cm is sufficiant for the standard setup (on the frame, the vertical saddle bar)
- 2 hose ends
- 1 derailleur cable adjuster
- A sensor (the same type as used for simple speed sensors of bike computers)
- A (strong) ring magnet that you can mount to the magnet holder
Electronics & related
- Arduino Nano board
- Servo (we recommend the PowerHD 1501MG)
- Toggle switch with function (on)off(on). This is just for testing and setup. You can replace this with two push-buttons if you like.
- Two PCB boards with “island contacts”.
- For the main circuit you need a 15x20 hole board
- For the control unit you need a 5x14 hole board
- 2 resistors 1/4W: 470 ohm
- 1 resistor 1/4W: 220 ohm
- A push-button with built-in LED (Pic 18)
- 1 mini-buzzer 5V
- About 50 cm of solid wire to solder the contact lines on the PCB’s (small diameter is OK)
- About 20 cm of flexible wire to connect the plugs and switches. Best is to use the coloured flatcable type (6-pole), diameter 0.75mm or even smaller. You need a larger diameter for the strong-current connections (1mm minimum)
- Some shrink-tube or isolation tape
- Two battery packs 2200mAh size AA, we recommend Ni-Mh:
- 5-cell (6V)
- 2-cell (2.4V)
- Battery charger (Ni-Mh) capable of charging 7-cell battery packs (8.4V), preferably with a discharge function.

- A 4-pole cable that connects the control unit to the BigBox. For a standard installation a length of 180 cm should do it. Telephone cable is just fine.
- A 3-pole servo connector. You can use “row pin” connectors for these as well.
- Plugs:
- Mono jack 3.5mm: 1 male plug to connect to the reed sensor, 1 female chassis type (Pic 19)
- Stereo jack 3.5mm: 1 male plug to connect to the test toggle switch, one female PCB-mounting type
- Charger plug: chassis type 5.5x2.5 (recommended) (Pic 20)
- Double pole contact switch “Key Switch” suitable for minimum 3A@9V (Pic 21)
- DIN 4-pole: 1 female plug to connect to the wire coming from the control unit, 1 male chassis (Pic 22)
- 4 screw terminals
- Tie-wraps: two strong ones (4mm, these will secure the 500gr weighing BigBox) and approx. 4 small ones
- 3 rubber bands, the kind that are being used to mount bike computers and such. You need 2 for the Control Unit and 1 for the Sensor.

Board specifications (Arduino or similar)
- Digital inputs: 3
- Digital outputs: 3 (1 with PWM output)
- Input voltage: 9V

Servo specifications (recommended)
- Torque: >16kg/cm
- Operating voltage: 6V
- Rotation >140°

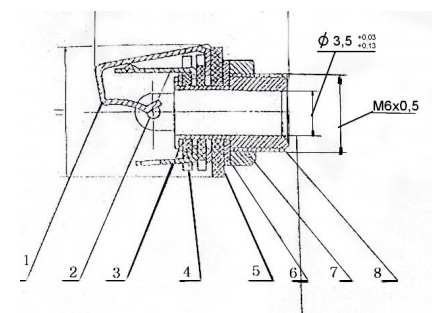
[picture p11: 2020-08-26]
installation/pics_18-22/Pic_19.JPG

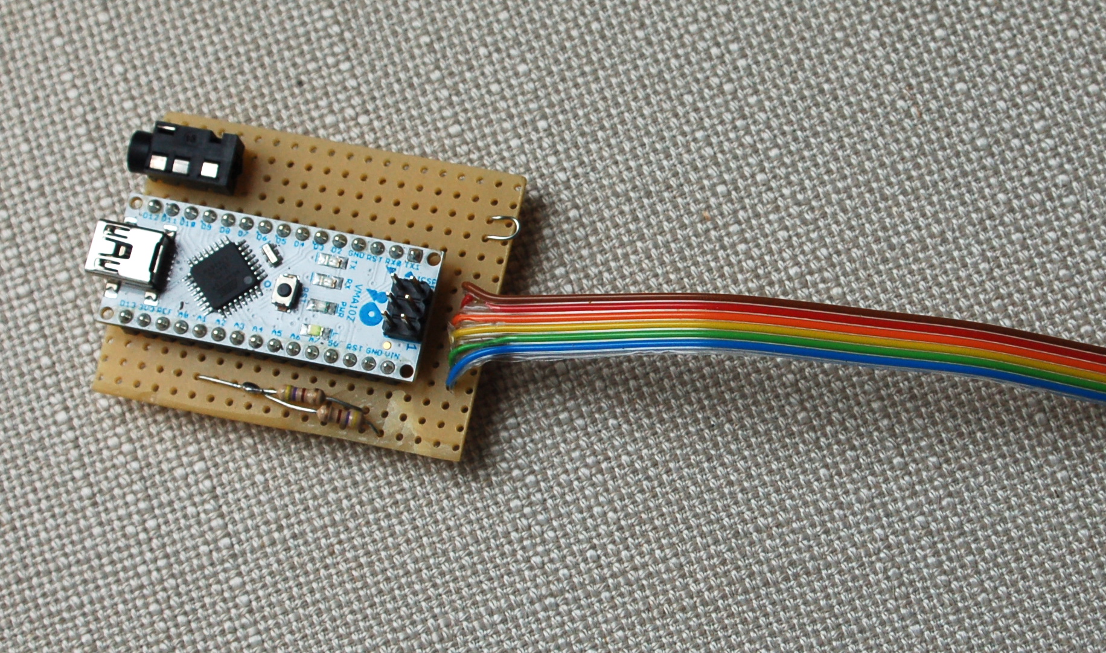
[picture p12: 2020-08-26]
installation/pics_1-17-building-manual/Pic_4.JPG

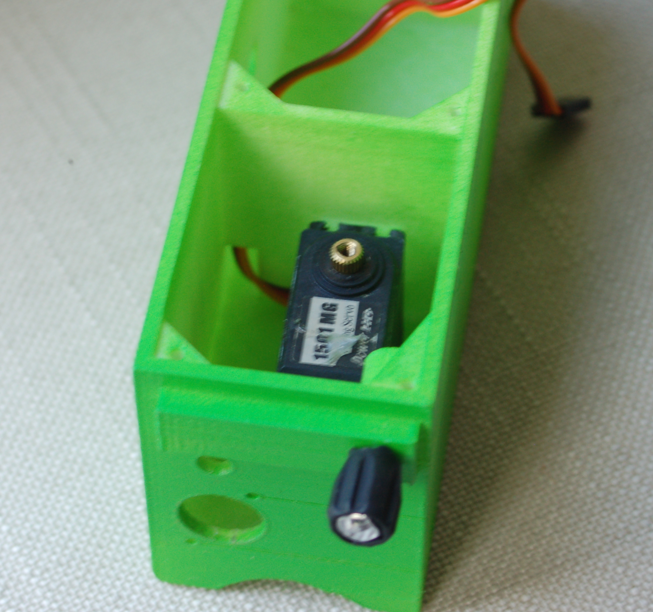
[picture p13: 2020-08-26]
installation/pics_1-17-building-manual/Pic_8.JPG

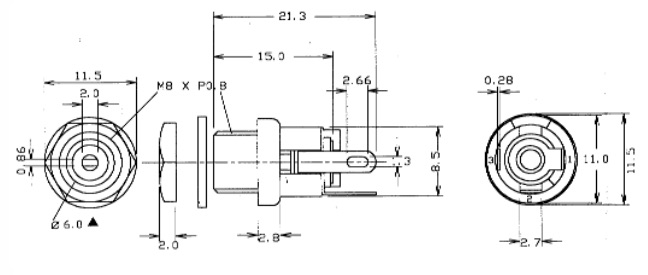
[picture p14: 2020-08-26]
installation/pics_18-22/Pic_20.JPG

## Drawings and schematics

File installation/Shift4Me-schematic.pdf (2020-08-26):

# Shift4Me schematic dated feb 19, 2020

–

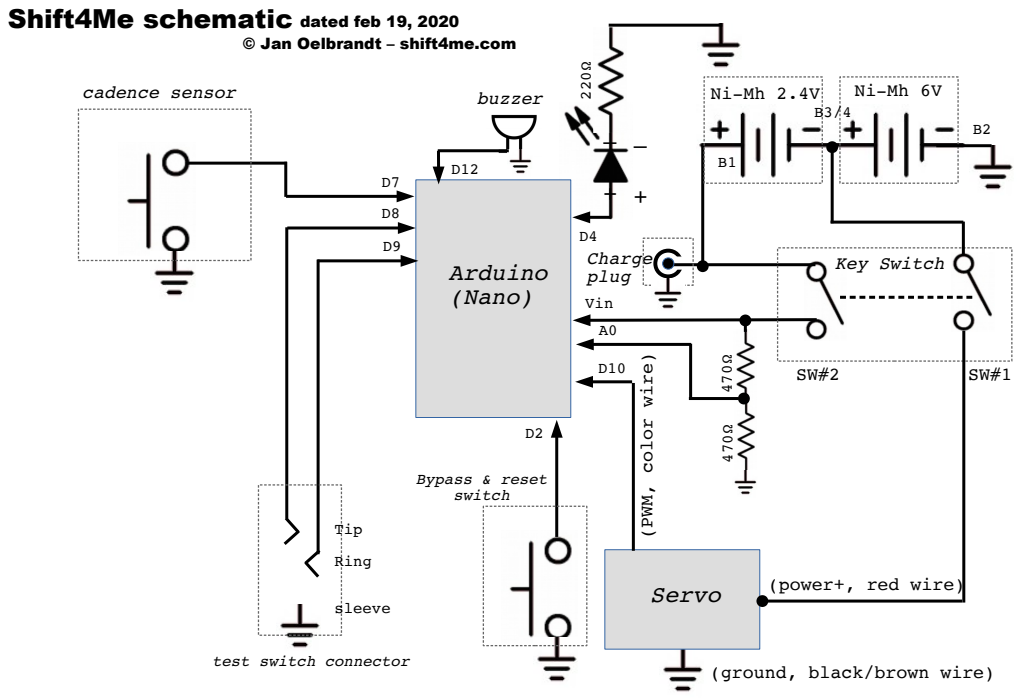
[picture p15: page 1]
Arduino (Nano); cadence sensor; Charge plug; Servo; Bypass & reset switch; Tip; Ring; sleeve; Key Switch; buzzer; Vin

© Jan Oelbrandt – shift4me.com

(power+, red wire)

test switch connector

(ground, black/brown wire)

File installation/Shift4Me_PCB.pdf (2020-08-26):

## Shift4me

V1.0

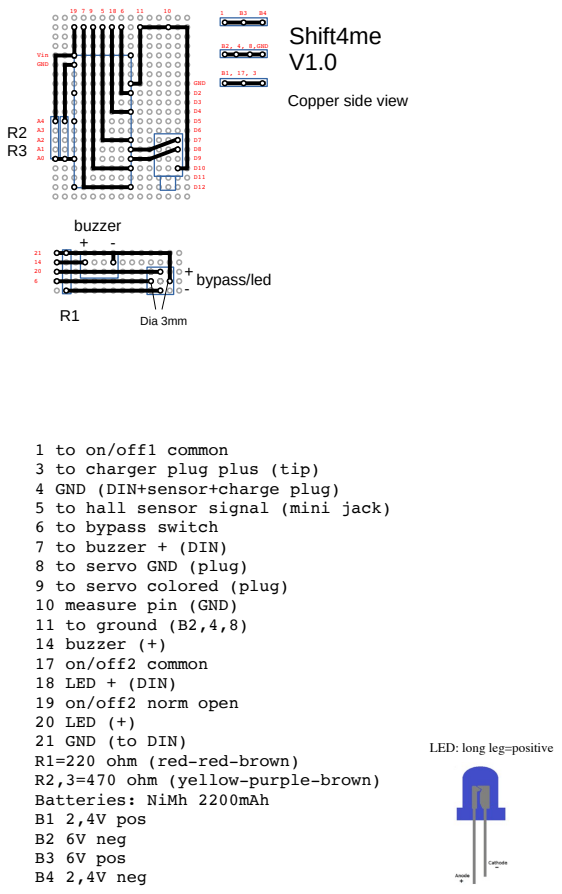
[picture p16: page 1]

1 to on/off1 common
3 to charger plug plus (tip)
4 GND (DIN+sensor+charge plug)
5 to hall sensor signal (mini jack)
6 to bypass switch
7 to buzzer + (DIN)
8 to servo GND (plug)
9 to servo colored (plug)
10 measure pin (GND)
11 to ground (B2,4,8)
14 buzzer (+)
17 on/off2 common
18 LED + (DIN)
19 on/off2 norm open
20 LED (+)
21 GND (to DIN)
R1=220 ohm (red-red-brown)
R2,3=470 ohm (yellow-purple-brown)
Batteries: NiMh 2200mAh
B1 2,4V pos
B2 6V neg
B3 6V pos
B4 2,4V neg

LED: long leg=positive

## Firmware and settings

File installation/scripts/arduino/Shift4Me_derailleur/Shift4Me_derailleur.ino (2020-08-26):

// Shift4Me script v.1.0 (for schematic feb 19 2020)
// written to control an Arduino Nano board (or 100% compatible) 
// feb 24, 2020
// original author: Jan Oelbrandt / Shift4me.com
// contact: info@shift4me.com - +3254503538

// THIS SOFTWARE IS DISTRIBUTED UNDER A GPL LICENSE - see bottom of script for all terms and conditions
///////////////////////////////////////////////////
// there are a bunch of USER CONFIGURABLE PARAMETERS on the three TABS
// please the notes on the seperate TABS to see what each parameter does, before you change anything

// DO NOT CHANGE THE FOLLOWING CODE (unless you know what you're doing)

int Frequency;
int ToleranceHigherGear;
int ToleranceLowerGear;
int ChangeDelayHeavy;
int ChangeDelayLight;
int HiLoAmount;
int MaxTurns;
String UseBuzzer;
String UseLed;

#include <Servo.h>
Servo myservo;

int RPM;
int FrequencyCount;
int ButtonDebounce = 250;
int ButtonDebounceShort = 50;
//int ReleaseTime;
unsigned long previousMillis = 0;
int pos;    // variable to store the servo position - taken from array of gears
int GearAmount;
int CorrectAmount;
int prev_pos;
int ActiveGear;
int buttonRed = 9;  // to force to a smaller sprocket
int buttonGreen = 8; // to force to a larger sprocket
int Sensor = 7;     // reads the hall sensor on/off value
int buttonBypass = 2; // reads the Bypass button
int buzzer = 12; //buzzer to arduino pin 12
String action = "none";
unsigned long currentMillis;
unsigned long refTime;
boolean SensorOverride = false;
int correctFrequency = 0;
int ledPin = 4; // led-connection (on/off and battery status)
int  sensorValue; // analog voltage sensing at pin Vin
float  Voltage; // convert sensorvalue voltage to 5V max
int Cycles = 0;
unsigned long pressTime;
String mode;
String Act = "no";

void setup() {
myservo.attach(10);  // attaches the servo 
pinMode(buttonRed, INPUT_PULLUP); // connects the manual override button (shift to smaller sprocket)
pinMode(buttonGreen, INPUT_PULLUP); // connects the manual override button (shift to larger sprocket)
pinMode(buttonBypass, INPUT_PULLUP); // connects the bypass button
pinMode(Sensor, INPUT_PULLUP);    // connection of the hall sensor
pinMode(ledPin, OUTPUT); // led-connection (on/off and battery status)
pinMode(buzzer, OUTPUT); // Set buzzer output
Serial.begin(9600);
// load derailleur data
  CorrectAmount = LoadSprocketWidth("CorrectAmount",0);
  GearAmount = LoadSprocketWidth("GearAmount",0);
  pos = LoadSprocketWidth("GetGear",99);
  ActiveGear = LoadSprocketWidth("StartingGear",0);
prev_pos = pos;
// load preferences
  Frequency = LoadRidePrefs("Frequency");
  ToleranceHigherGear = LoadRidePrefs("ToleranceHigherGear");
  ToleranceLowerGear = LoadRidePrefs("ToleranceLowerGear");
  ChangeDelayHeavy = LoadRidePrefs("ChangeDelayHeavy");
  ChangeDelayLight = LoadRidePrefs("ChangeDelayLight");
  HiLoAmount = LoadRidePrefs("HiLoAmount");
  MaxTurns = LoadRidePrefs("MaxTurns");
  UseBuzzer = LoadSignalPrefs("UseBuzzer");
  UseLed = LoadSignalPrefs("UseLed");
// change 24 feb, was before: myservo.writeMicroseconds(pos);
PerformReset();

Serial.print("Starting in position: ");
Serial.print(pos);
Serial.print(", gear number ");
Serial.println(ActiveGear+1);

unsigned long currentMillis = millis();
Serial.println(currentMillis);
previousMillis = currentMillis;
refTime = currentMillis;
digitalWrite(ledPin, HIGH); 

}

void loop() 
{

// correct if button actions (MANUAL OVERRIDE)
   if(digitalRead(buttonRed)==LOW)
    {
    action = "less";
    SensorOverride = true;
    delay(ButtonDebounce);
    }
   if(digitalRead(buttonGreen)==LOW)
    {
    action = "more";  
    SensorOverride = true;
    delay(ButtonDebounce);
    }
    if(digitalRead(buttonBypass)==LOW) {
      pressTime = millis();
     // delay(ButtonDebounce);
      BypassButton(pressTime);
Serial.print("mode: ");
Serial.println(mode);
    if(mode == "bypass") {
    action = "none";  
    SensorOverride = true;
    }
    else if(mode == "reset") {
      SensorOverride = true;
      action = "reset";  
    }
    
    }
    else {
      mode = "normal";
    }
// if max Cycles is exceeded
   if(Cycles > MaxTurns) {
  //  action = "less";
    SensorOverride = true;
    Serial.println("MAX TURNS EXCEEDED");
    //  Serial.println(RPM);
   }

// count rotation
currentMillis = millis();

if(digitalRead(Sensor)==LOW || SensorOverride == true)
{
    if(digitalRead(Sensor)==LOW) {
Serial.println("hall triggered");
      Cycles = Cycles + 1;
     //currentMillis = millis();
     FrequencyCount = currentMillis - previousMillis;
      delay(ButtonDebounce);
      previousMillis = currentMillis;    
      // 1000 milliseconds, 60 seconds
      RPM = 60000/FrequencyCount;
    //    Serial.print("actual RPM: ");
    //  Serial.println(RPM);

// if RPM exceeds limits

  // turning too fast, so move to smaller sprocket
if((RPM - ToleranceHigherGear)>(Frequency)) {
  action = "less";
  // Serial.println("HALL TRIGGERED less");
  }
  // turning too slow, so move to larger sprocket
  else if((RPM + ToleranceLowerGear)<(Frequency)) {
      action = "more";
    //  Serial.println("HALL TRIGGERED more");   
 }
 else {
  action = "none";
 }
//} // THIS WAS HERE BEFORE v1.1.7
// else if((refTime + ChangeDelay)<currentMillis){
//  action = "none";
// }

// if RPM is too low (stalling): take no action
      if(RPM < 15) {
    //  if(FrequencyCount>3000) {
    //  if(FrequencyCount>6000) {
         action = "none";
         Serial.println("STALLING");
         // RESET
         // prev_pos = pos;
          RPM = 0;
          refTime = currentMillis;
          Cycles = 0;

      }   
// if RPM is too high (pedal stalls at hall sensor): take no action
       if(RPM > 200) {
         action = "none";
      }   

      
    }
//Serial.println(Cycles);
   
// process action if ChangeDelay time has passed since last change
// if buttonBypass is not pushed
if(  ( (refTime + ChangeDelayHeavy)<currentMillis || SensorOverride == true) && digitalRead(buttonBypass)==HIGH ) {


if(action == "less") {
  Act = "yes";
  // move to smaller sprocket
  ActiveGear = ActiveGear-1;
  pos = LoadSprocketWidth("GetGear",ActiveGear);
  

  // correct if below zero gear
  if (ActiveGear < 0) { ActiveGear = 0; action = "none"; pos = LoadSprocketWidth("GetGear",ActiveGear); }
  else{
    pos = pos - (CorrectAmount/4);
    
   if(UseLed == "yes") {
    digitalWrite(ledPin, HIGH);
   }
   if(UseBuzzer == "yes"){
BuzzerHeavyGear ();
        }
     }
}
}
if(  ( (refTime + ChangeDelayLight)<currentMillis || SensorOverride == true) && digitalRead(buttonBypass)==HIGH ) {

if(action == "more") {
  Act = "yes";
  // move to larger sprocket
   ActiveGear = ActiveGear+1;
   pos = LoadSprocketWidth("GetGear",ActiveGear);
  pos = pos + CorrectAmount;
     // correct if above derailleur maximum
  if (ActiveGear > (GearAmount-1)) { ActiveGear = GearAmount-1; action = "none";   pos = LoadSprocketWidth("GetGear",ActiveGear);
 // pos = pos + CorrectAmount;
  }
  else {
    if(UseLed == "yes") {
    digitalWrite(ledPin, HIGH);
   }
     if(UseBuzzer == "yes"){
    // send audio signal for light gear
BuzzerLightGear ();
     }
  }
  

}
if(mode == "reset") {
PerformReset();
   Act = "yes";
}
// new feb 24
if(mode == "bypass") {
delay(5000);
   Act = "no";
}
} //end of ChangeDelay cycles

if(Act == "yes"){ 
    Act = "no";
     myservo.writeMicroseconds(pos);  

     // moved to larger sprocket - delay a bit longer
      if(action == "more")  {
         pos = pos - CorrectAmount;
         delay(800);
         }

      // moved to smaller sprocket lesser CorrectAmount
      if(action == "less")  {
        pos = pos + (CorrectAmount/4);
         delay(400);
         }
      myservo.writeMicroseconds(pos);

         // display action every ChangeDelay and reset all
  // check battery voltage
  // read the input on analog pin 0 for the batteries (2.4V and 6V in series):
sensorValue = analogRead(A0);
  // Convert the analog reading (which goes from 0 - 1023) to a voltage (0 - 9V):
Voltage = sensorValue * (8.4 / 1023.0);
// flash LED if Voltage is too low
// at aprox 7V total, the 6V battery will be about 5.5V, it is too dropped to pull the servo
  if(Voltage<7){
  LowBatteryWarning();
  // correct time because of delaying of flashing LED
 // currentMillis = currentMillis + 240;
  }
  else {
    digitalWrite(ledPin, HIGH); 
  }
 Serial.println();
  Serial.print("battery voltage: ");
      Serial.println(Voltage);
      Serial.println();
      Serial.print("measured RPM: ");
      Serial.println(RPM);
      Serial.print("target RPM: ");
      Serial.println(Frequency+correctFrequency);
      Serial.print("action: ");
      Serial.println(action);
      if(mode != "normal"){
        Serial.print("button mode: ");
      Serial.println(mode);
      }
      Serial.print("now in gear number: ");
      Serial.print(ActiveGear+1);
      Serial.print(", pos is ");
      Serial.println(pos);

    prev_pos = pos;
    action = "none";
    RPM = 0;
    refTime = currentMillis;
    Cycles = 0;
    if(SensorOverride == true){
      refTime = refTime + 5000;
      Cycles = Cycles-5;
    SensorOverride = false;
    Serial.print(" - battery voltage: ");
      Serial.println(Voltage);
    }
 //   if(digitalRead(buttonBypass)==LOW){
 //     Serial.println("servo action BYPASSED");
 //   }
    
 } // end of processing
} // end of Sensor Loop 
} // end of loop
void BuzzerHeavyGear (){
  tone(buzzer, 2000); 
  delay(100);     
  noTone(buzzer);    
  delay(80);      
   tone(buzzer, 1500);
  delay(100);       
  noTone(buzzer);   
  delay(80);      
   tone(buzzer, 1000); 
  delay(100);       
 noTone(buzzer);    
  delay(300);        // delay to allow pedal force disengage
}
void BuzzerLightGear (){
  tone(buzzer, 2000); 
  delay(150);     
  noTone(buzzer);   
  delay(50);      
   tone(buzzer, 2220); 
   delay(50);       
  noTone(buzzer);   
  delay(20);     
   tone(buzzer, 2300); 
  delay(50);   
  noTone(buzzer);     
  delay(50);       
   tone(buzzer, 2220); 
   delay(50);     
   noTone(buzzer); 
  delay(400);        // delay to allow pedal force disengage
}
void LowBatteryWarning(){
   digitalWrite(ledPin, HIGH); 
  delay(100);      
  digitalWrite(ledPin, LOW); 
 // tone(buzzer, 2000); 
  delay(100); 
  digitalWrite(ledPin, HIGH); 
 // noTone(buzzer); 
  delay(100);      
  digitalWrite(ledPin, LOW); 
 // tone(buzzer, 2000); 
  delay(100); 
  digitalWrite(ledPin, HIGH); 
 // noTone(buzzer); 
  delay(100); 
  digitalWrite(ledPin, LOW); 
 // tone(buzzer, 2000); 
  delay(100); 
  digitalWrite(ledPin, HIGH); 
 // noTone(buzzer); 
  // correct time because of delaying of flashing LED
 // currentMillis = currentMillis + 240;
}
void PerformReset(){
  ActiveGear = LoadSprocketWidth("StartingGear",0);
   pos = LoadSprocketWidth("GetGear",99);
   pos = pos + CorrectAmount;
   myservo.writeMicroseconds(pos);
         delay(200);
   pos = pos - CorrectAmount;
   myservo.writeMicroseconds(pos);  
}

String BypassButton(unsigned long var){
//int pressTime2 = pressTime;
int StopSound = 0;
unsigned long ReleaseTime;
delay(ButtonDebounceShort);
 while (digitalRead(buttonBypass) == LOW)
 {
// buzz shortly for bypass
if(StopSound == 0) 
  { 
     
    if (millis()>(var+500) ) {
      noTone(buzzer); 
   //   StopSound = 1;
    }
    else {
      tone(buzzer, 500);
    }
  } 
// if button is released buzz for reset
if (millis()>(var+2000) && StopSound == 0){
  noTone(buzzer); 
  delay(100); 
  tone(buzzer, 2000); 
  delay(50); 
  noTone(buzzer); 
  delay(50); 
  tone(buzzer, 1000); 
  delay(100); 
  noTone(buzzer); 
  StopSound = 1;
  }
 }
  ReleaseTime = millis();
  noTone(buzzer); 

delay(ButtonDebounceShort);

if (( ReleaseTime-2000 )<var){
  mode = "bypass";
  return mode;
}
else
{
  mode = "reset";
  return mode;
}
}
//        This program is free software: you can redistribute it and/or modify
//        it under the terms of the GNU General Public License v.3 as published by
//        the Free Software Foundation.

//        This program is distributed in the hope that it will be useful,
//        but WITHOUT ANY WARRANTY; without even the implied warranty of
//        MERCHANTABILITY or FITNESS FOR A PARTICULAR PURPOSE.  See the
//        GNU General Public License for more details.

//        For a full copy of the GNU General Public License
//        see <http://www.gnu.org/licenses/>

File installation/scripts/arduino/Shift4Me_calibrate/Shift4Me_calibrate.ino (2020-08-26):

  
#include <Servo.h>      // include the servo working (send pulses)

Servo myservo;  // create servo object to control a servo

int buttonMin = 9;      // connects the LOWER-button to pin 9
int buttonMax = 8;      // connects the HIGHER-button to pin 8
String action = "none"; // action of servo on startup
int MS = 550;          // position of the servo on startup
int AmountMs = 50;      // travel of the servo per button press
int ServoMax = 2400;    // max position of the servo
int ServoMin = 500;     // min position of the servo
int ledPin = 4; // led-connection (on/off and battery status)
int  sensorValue; // analog voltage sensing at pin Vin
float  Voltage; // convert sensorvalue voltage to 5V max


void setup() 
{

MS = ServoMin;
  
myservo.attach(10);  // attaches the servo on pin 10 to the servo object
pinMode(buttonMin, INPUT_PULLUP); 
pinMode(buttonMax, INPUT_PULLUP);
Serial.begin(9600);   // active readout
myservo.writeMicroseconds(MS); // send pulses to the servo
pinMode(ledPin, OUTPUT); // led-connection (on/off and battery status)
digitalWrite(ledPin, HIGH); 
}

void loop() // master loop of the script
{
   action = "none";

   if(digitalRead(buttonMin)==LOW)  // what to do when the LOWER-button is pressed
    {
    delay(200);          // delay for button debounce
    MS = MS - AmountMs;  // lower the pulses by the pre-set amount           
    action = "Min";       // the name of this action
    }
  
   
       if(digitalRead(buttonMax)==LOW) // what to do when the HIGHER-button is pressed
    {
    delay(200);          
    MS = MS + AmountMs;
    action = "Plus";
    }
    
// display action if one of the buttons is pressed 
    if(action == "Min" || action == "Plus")
    {
        // check battery voltage
  // read the input on analog pin 0 for the batteries (2.4V and 6V in series):
sensorValue = analogRead(A0);
  // Convert the analog reading (which goes from 0 - 1023) to a voltage (0 - 9V):
Voltage = sensorValue * (8.4 / 1023.0);
// flash LED if Voltage is too low
// at aprox 7V total, the 6V battery will be about 5.5V, it is too dropped to pull the servo
  if(Voltage<7){
  digitalWrite(ledPin, HIGH); 
  delay(100);      
  digitalWrite(ledPin, LOW); 
  delay(100); 
  digitalWrite(ledPin, HIGH); 
  delay(100);      
  digitalWrite(ledPin, LOW); 
  delay(100); 
  digitalWrite(ledPin, HIGH); 
  delay(100);      
  digitalWrite(ledPin, LOW); 
  delay(100); 
  digitalWrite(ledPin, HIGH); 
  // correct time because of delaying of flashing LED
 // currentMillis = currentMillis + 240;
  }
  else {
    digitalWrite(ledPin, HIGH); 
  }
      // after battery check, see if the max or min are not met
      if(MS > ServoMax){
        Serial.println("you reached the maximum of the servo");
        MS = MS - AmountMs;
      }
      else if (MS < ServoMin){
        Serial.println("you reached the minimum of the servo");
        MS = MS + AmountMs;
      }
      // if all is ok, continue
      else {
         Serial.println();

      Serial.println();
      Serial.print("servo pulsewidth: "); // display the pulse text
      Serial.print(MS);                 // display the amount
        Serial.print(" // battery voltage: ");
      Serial.println(Voltage);
        myservo.writeMicroseconds(MS);    // send the pulse to the servo
      }
      
    }
  
}

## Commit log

2020-08-26 initial init
    [BigBox.stl, ControlUnit.stl, MagnetHolder.stl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]
2020-08-29 extend Shift4Me-basic-components sheet w/ an alternative electronics supplier which reduce the electronics cost to ~95€ instead of 145€
    [Shift4Me-basic-components.ods]
2020-08-30 Update README.md
    Add chip.de news link
2020-08-31 extend Shift4Me-basic-components sheet w/ Power HD LF-20MG low energy digital servo
    [Shift4Me-basic-components.ods]
